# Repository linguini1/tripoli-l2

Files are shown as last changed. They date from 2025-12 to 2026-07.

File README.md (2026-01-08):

# Tripoli L2 Certification Rocket

<p align="center">
    
    <br/>
    Mission Patch
</p>

This repository contains the design files for my Tripoli L2 certification
rocket. My desire is to publicize the design files with a free-to-access intent
such that others in the rocketry hobby can benefit from them.

<p align="center">
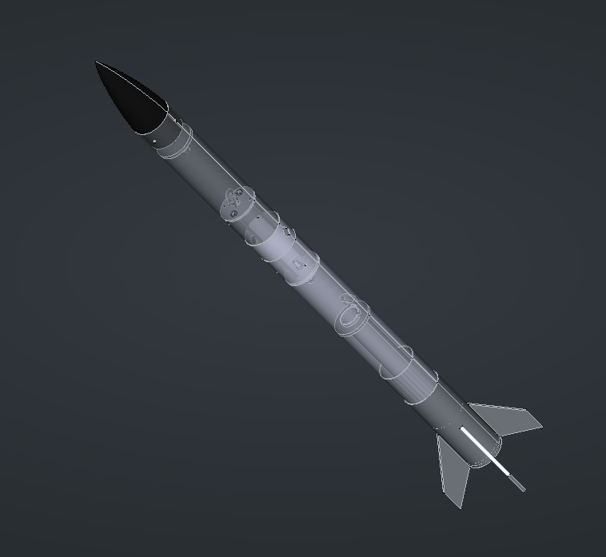
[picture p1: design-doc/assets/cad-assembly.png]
    
    <br/>
    Tripoli L2 CAD Assembly
</p>

## Design Document

The primary design document is located in the [design-doc
directory](./design-doc). It contains the requirements, design and analysis of
the rocket along with some design files in a cohesive layout.

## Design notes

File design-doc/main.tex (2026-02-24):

\documentclass[11pt]{article}

\def\doctitle{Analysis and Design of a Tripoli L2 Certification Rocket}

\usepackage{amssymb}
\usepackage{amsmath}
\usepackage{float}
\usepackage{graphicx}
\usepackage{listings}
\usepackage{enumitem}
\usepackage[
    pdftitle={\doctitle},
    colorlinks=false,
    allbordercolors={0 0 0},
    citebordercolor={1 1 1}, % No border for citations %
    pdfborderstyle={/S/U/W 1},
    linktoc=all,
]{hyperref}
\usepackage[nameinlink]{cleveref} % For hyperlinked references
\usepackage[letterpaper, margin=1in]{geometry}

% Add bibliography in IEEE
\usepackage[style=ieee]{biblatex}
\addbibresource{bibliography.bib}

% Add glossary entries
\usepackage[acronym,nogroupskip,nonumberlist]{glossaries}
\input{sections/glossary.tex}
\makeglossaries

% Remove paragraph indentation and use newline to separate instead. %
\usepackage[parfill]{parskip}
\setlength{\parindent}{0cm}

\title{\doctitle}
\author{
    Matteo Golin \\
    \texttt{matteo.golin@gmail.com}
}
\date{
    Created: December 27, 2025 \\
    Updated: \today
}

\begin{document}

% TITLE

\maketitle
\begin{center}
    
\end{center}
\pagebreak

% ABSTRACT

\input{sections/abstract.tex}
\pagebreak

% FRONT MATTER

{
	% No link styling in the TOC
	\hypersetup{hidelinks}
	\tableofcontents
	\pagebreak
	\listoffigures
	\pagebreak
	\listoftables
}
\pagebreak

% INTRODUCTION

\input{sections/introduction.tex}

% SECTIONS

\input{sections/requirements.tex}
\input{sections/overview.tex}
\input{sections/design/design.tex}
\input{sections/bom.tex}

\pagebreak

% GLOSSARY

\printglossary[title={Glossary}]
\printglossary[type=\acronymtype,title={Acronyms}]
\pagebreak

% BIBLIOGRAPHY

\printbibliography
\pagebreak

% APPENDIX

\input{appendix/index.tex}

\end{document}

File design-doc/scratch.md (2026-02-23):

# Scratch Ideas

## Motor

38mm motor is the final choice. It is easier to obtain in Canada and will also
be cheaper.

The motor needs a retention method. Based on what I've heard from others who
have done an L2, a retention method similar to an Aeropack retainer (like my L1)
is suitable.

## Recovery

Dual deploy, dual break. Drogue at apogee, main halfway down. Switchband coupler
to house deployment avionics, which will consist of between \[1, 2\] barometric
altimeters capable of deploying 2 deployment charges each (main and drogue) at
different altitudes. Altimeters will also need to be capable of deploying after
a set time-limit as an extra precaution.

Deployment will use black-powder charges detonated by e-matches.

## Airframe

Nosecone is PETG 3D-printed. Body tubes are fiberglass sock layup (6 layers,
light, 3in). Fins will be plywood through-wall so that I can have better thrust
transfer. Other materials are acceptable if I can acquire them.

[Fiberglass sock](https://sollercompositesllc.com/product/natural-uncolored-3-light-fiberglass-sleeves/)

I will have 2x 36" cardboard mandrels for the layup. The airframe body tubes
are:
* Forward: 14in
* Aft: 26in
* Switch-band exterior: 2in

In order to waste less sock, I will have one 18in mandrel for the forward +
switch-band layup. Then, I will use a 28in mandrel for the aft tube (inch of
slack on either end). Then there is an 8in coupler section for which I will
3D-print a 10in mandrel (to get the correct dimensions to be a coupler).

$18 + 28 + 10 = 56$ inches of total tube length. $58 \times 6$ for 6 layers gives
336 inches of sock required (28 ft). I will probably want to buy at least 30ft
(since that gives a discount on Soller anyways), but I may also want to account
for a complete screw-up on one of the tubes (let's say the coupler, since that
will be my test-tube). That would amount to 420in or 35 ft of stock.

## Avionics

\[1,2\] barometric altimeters for recovery deployment. Must perform on-board
altitude/charge detonation logging, be capable of firing two deployment charges
each and have some kind of audio indicator of arming and continuity check.

The avionics bay must be capable of supporting a redundant deployment
configuration.

The GPS tracker will go in the nosecone and at minimum must be capable of
providing coordinates of the rocket's landing location over long-range radio.

# Parts

* [Motor mount tube](https://www.allrockets.ca/Build/Motor-Tubes/P/38)
* [Motor retainer (for specific motor mount tube)](https://www.allrockets.ca/Build/Motor-Retainers/38-mm-P)
* [Eyebolts x4](https://www.allrockets.ca/Build/Swivels-Links/Eye-Bolt-1)
* [Rail buttons](https://www.allrockets.ca/Build/Rail/Delrin-Rail-Gudes/1010-Airframe)
* [Body tube (for layup) x2](https://www.allrockets.ca/Build/Body-Tubes/30)
* [12in drogue](https://www.allrockets.ca/Build/Parachutes/Nylon-Red-12?cPath=19_212&)
* [36in main](https://www.allrockets.ca/Build/Parachutes/36)
* [Kevlar shock cord (?m)](https://www.allrockets.ca/Build/Shock-Cords/Kevlar-1500)
* [12x12 chute protector x2](https://www.allrockets.ca/Accessories/Chute-Protector-12)
* [1kg black PETG](https://www.amazon.ca/ELEGOO-Filament-Printing-Dimensional-Cardboard/dp/B0CMC8CDFN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)
* [10-24x12in threaded rod x2](https://www.homedepot.ca/product/paulin--10-24-x-12-inch-fully-threaded-steel-rod-zinc-plated-unc/1000798814)

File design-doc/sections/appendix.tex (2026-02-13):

\section{Technical Drawings}

These are the technical drawings that describe the dimensions of each rocket
component needed for assembly.

\subsection{Nosecone}

\begin{figure}[H]
	\centering
	
	\caption{Technical drawing of the nosecone model}
\end{figure}

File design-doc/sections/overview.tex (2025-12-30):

\section{Design Overview}

This rocket will be a dual break, dual deploy rocket. It is technically only
necessary to have a single-break, single-deploy system, but this design choice
will teach me more about what's required for an L3 certification as well as
reduce any ability for the rocket to drift after apogee.

Since the rocket is dual break, the design for the avionics bay is going to be a
switch-band. This is a common choice for dual-deploy rocket and also looks very
simple to integrate (to me). Since the entire switch-band assembly is removable,
it will be easy to fiddle with when installing the avionics and can be replaced
entirely if I do something silly like drill the arming holes terribly wrong or
discover I need to re-arrange the entire avionics section. The primary
inspiration for the design the switchband avionics section is the design from
Joe Barnard's \textit{Send It!} rocket. \cite[\nopp 4:14]{bps-sendit} I like
the design choice of using Wago lever connectors for deployment charges to avoid
a screwdriver \cite[\nopp 5:47]{bps-sendit}, but I will need to come up with a
better solution than just epoxying the connectors to the bulkhead in case one
needs to be replaced. The bulkheads will be pressure sealing in order to prevent
the deployment charges from affecting the barometric altimeters inside the
avionics bay, and also to make sure that the correct volume of the rocket is
pressurized to deploy the chutes. Most of the configurations I have seen use a
small lip on both bulkheads so that they rest on the switchband coupler tube. I
have been told that using a o-ring to seal the pressure is overkill.

\begin{figure}[H]
	\centering
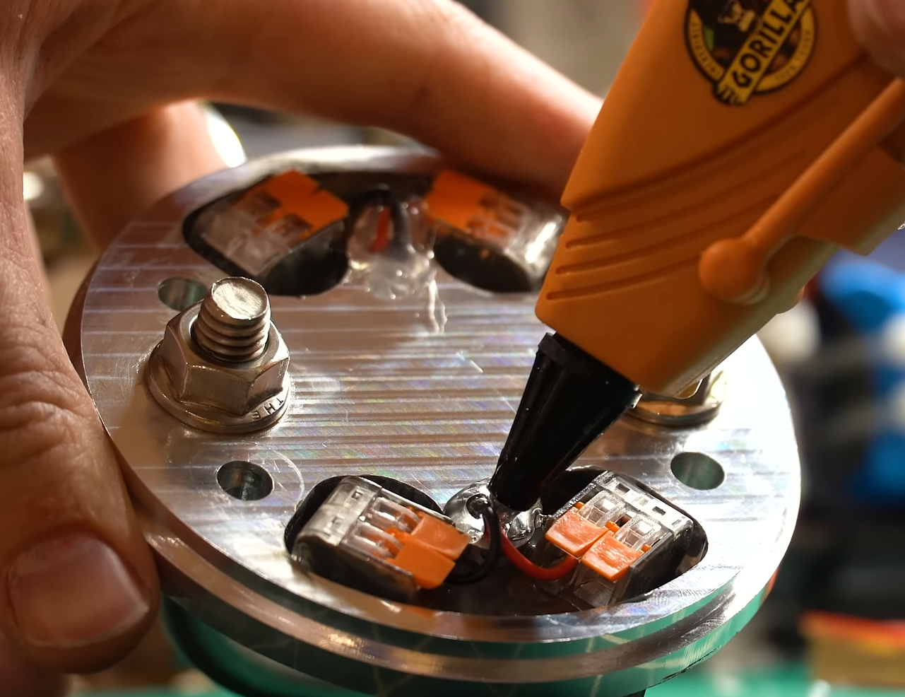
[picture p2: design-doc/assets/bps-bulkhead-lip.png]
	
	\caption{Aluminum bulkhead for switchband with a visible lip for the coupler
    tube \cite[\nopp 6:17]{bps-sendit}}
\end{figure}

For deployment electronics, I will not fly a redundant configuration if I can
help it (the Tripoli L2 rules do not require it \cite{tripoli-l2}) in order to
save costs, but I would like the avionics bay design to be capable of supporting
a redundant configuration if necessary. This should mostly be an issue of wiring
and extra space in the avionics bay, so it is unlikely to be a large
undertaking.

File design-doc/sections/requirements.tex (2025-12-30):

\section{Design Requirements}

The primary requirements for the rocket are derived from the Tripoli L2
certification requirements in \cite{tripoli-l2}, the L2 experience flight
requirements as per \cite[\nopp 4]{tripoli-l3} and the Tripoli Unified Safety
Code. \cite{tripoli-safety} These requirements are critical to meet in order to
achieve the goal of this rocket, which is to obtain my L2 certification and
complete the experience requirements towards an L3.

The secondary requirements for the rocket are derived from the desire to lower
the risk of failing the certification process and to reduce the amount of effort
required for assembly, pre-flight preparation and post-flight recovery.

The tertiary requirements for the rocket are derived from the desire to learn
some new skills and have a somewhat cool certification rocket to be proud of.
These requirements can be given up, just at my own disappointment.

\subsection{Primary Requirements}

\begin{enumerate}[label={R 1.\arabic*}]
	\item The rocket must be of conventional design (stabilized by fins and
	      recovered under parachutes) \cite[Airframe]{tripoli-l2}
	\item The rocket must be not be entirely 3D printed \cite[Airframe]{tripoli-l2}
	\item The rocket must be recovered by parachute \cite[Recovery]{tripoli-l2}
	\item The rocket must have a descent rate less than 11 meters per second
	      \cite[\nopp 11-1]{tripoli-safety}
	\item The rocket's recovery deployment must be electronically controlled
	      \cite[4]{tripoli-l3}
	\item All components of the rocket must be connected and recovered in one
	      assembly \cite[Non-Certification]{tripoli-l2}
	\item The rocket must be powered by a single J, K or L motor \cite[Motor]{tripoli-l2}
	\item The rocket must have a thrust to weight ratio of 5:1 or more \cite[\nopp 7-1.4]{tripoli-safety}
	\item The rocket must have a stable ascent \cite[Certification Flight]{tripoli-l2}
	\item The rocket must have a marked center of pressure \cite[7-1.2]{tripoli-safety}
	\item The rocket must have a marked center of gravity \cite[7-1.2]{tripoli-safety}
\end{enumerate}

\subsection{Secondary Requirements}

\begin{enumerate}[label={R 2.\arabic*}]
    \item The rocket must fly a 38mm motor
	\item The rocket must be capable of recovery deployment both via motor
	      ejection charge and electronic control, under the assumption that both
	      fire during flight.
	\item Continuity of deployment charge channels must be verifiable at the
	      time of arming on the pad.
	\item The rocket must have a GPS tracker so that its final landing location
	      can be obtained while tracking its flight from the vertical launch area.
	\item The deployment altimeter must be equipped with a barometer for
	      higher accuracy altitude estimation.
	\item The deployment system must be capable of firing deployment charges
	      both at a specific altitude and after a fixed time since lift-off in
	      the case of failure to detect altitude.
	\item The GPS tracker frequency must be capable of being easily changed on
	      the pad.
	\item The deployment altimeter must log timestamped altitude measurements
	      during flight.
	\item The deployment altimeter must log timestamped deployment event
	      signals.
	\item All locations for connecting shock-cord which need to be accessed
	      during pre-flight preparation must be easily accessible by hand.
	\item Rail buttons must be capable of being installed using the provided
	      flanges.
	\item One rail button must be placed as low as possible on the rocket
	      airframe, and the other must be placed at the expected center of
	      gravity.
	\item The GPS tracker must have a transmission range that exceeds the
	      maximum expected drift of the rocket.
	\item All 3D printed parts and assembly tools must be printable on a
	      $220\times220\times250$ mm print bed.
	\item The deployment electronics bay must have sufficient venting holes
	      for access to the atmosphere during flight.
	\item All separate volumes of the rocket must have sufficient venting holes
	      to prevent unintended separation.
	\item The rocket avionics bay must be capable of supporting a redundant
	      deployment configuration.
\end{enumerate}

\subsection{Tertiary Requirements}

\begin{enumerate}[label={R 3.\arabic*}]
	\item At least one part of the airframe should be made of a composite material
	      (either fiberglass or carbon fiber is acceptable)
	\item No fastener should be a Phillips head
	\item The rocket should be easy to manufacture
    \item The rocket might have a boat-tail
\end{enumerate}

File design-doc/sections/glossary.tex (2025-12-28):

\newacronym{pcb}{PCB}{Printed Circuit Board}

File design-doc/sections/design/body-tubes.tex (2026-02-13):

\subsection{Body Tubes}

The body tubes for the rocket are 3in diameter and made of fiberglass composite.

\subsubsection{Manufacture}

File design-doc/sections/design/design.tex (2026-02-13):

\section{Design}

\input{sections/design/nosecone.tex}
\input{sections/design/body-tubes.tex}
\input{sections/design/switchband.tex}
\input{sections/design/fincan.tex}
\input{sections/design/recovery.tex}
\input{sections/design/avionics.tex}

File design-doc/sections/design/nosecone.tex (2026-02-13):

\subsection{Nosecone}

The nosecone is a Von Karmaan nosecone shape. The length of the nose is 7
inches, and the length of the shoulder is 2 inches. The shoulder thickness is
$\frac{1}{4}$ inch.

The height of the nosecone was selected to be within the ~225mm print-height
limit for most consumer printers.

\subsubsection{Manufacture}

The nosecone of the rocket will be manufactured out of PETG for simplicity. This
allows the (relatively complex) shape to be made on a consumer 3D printer, which
is generally accessible. It does not require an "advanced" 3D printer which has
the capability to print in filaments like ABS. PETG also has the property of
being radio transparent, which is required for a nose-cone GPS tracker.

The nosecone should be printed using gyroidal infill for high strength. It is
also recommended to use a minimum of 4 vertical walls in the slicer settings for
durability.

\subsection{Assembly}

The nosecone is affixed to the forward body tube using 4 radial M3 screws. The
nosecone is fitted with 4 heat-set inserts evenly space along the shoulder. This
allows the nosecone to be removed, but also tightly affixed for flight.

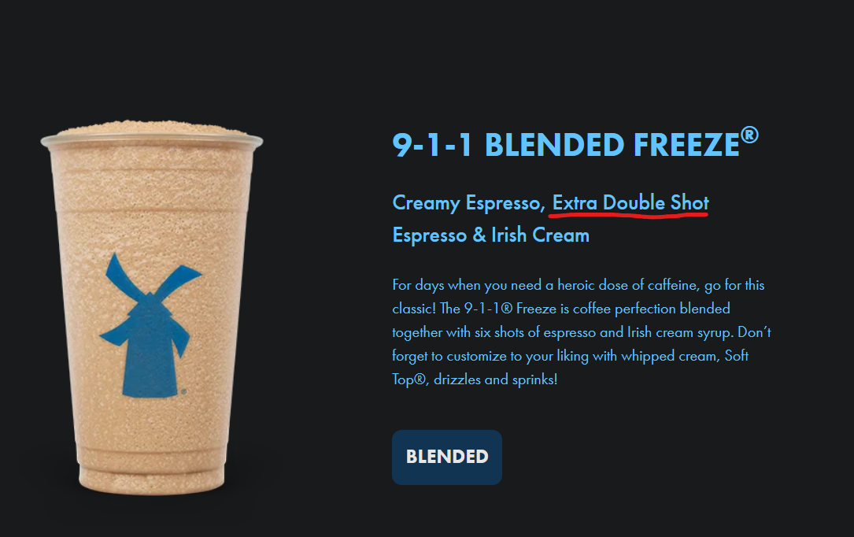
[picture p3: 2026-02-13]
design-doc/assets/dbros.png

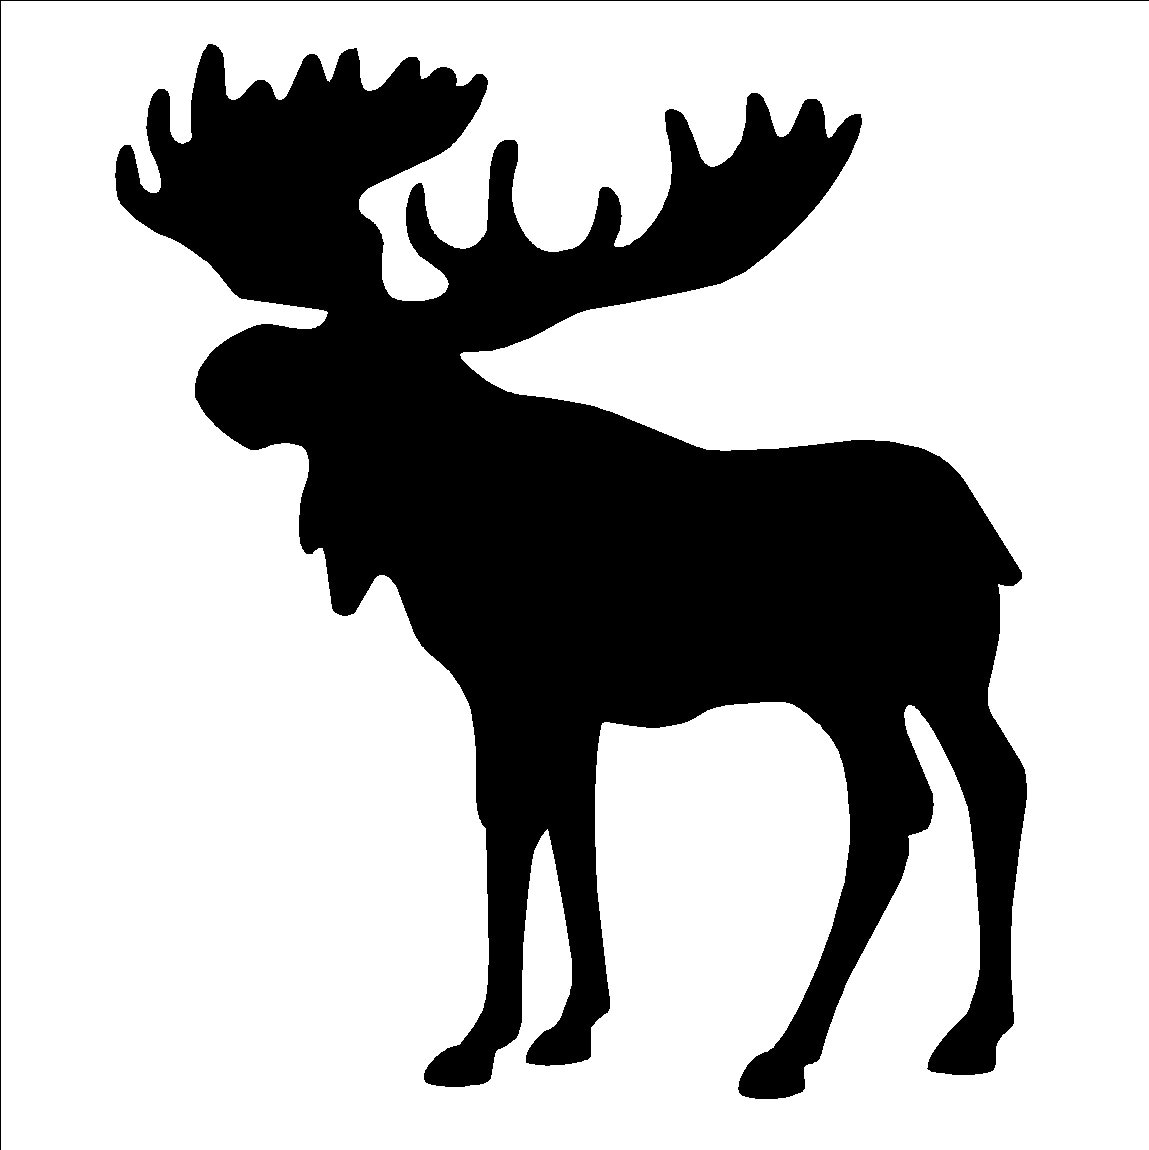
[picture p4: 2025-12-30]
livery/moose.jpg

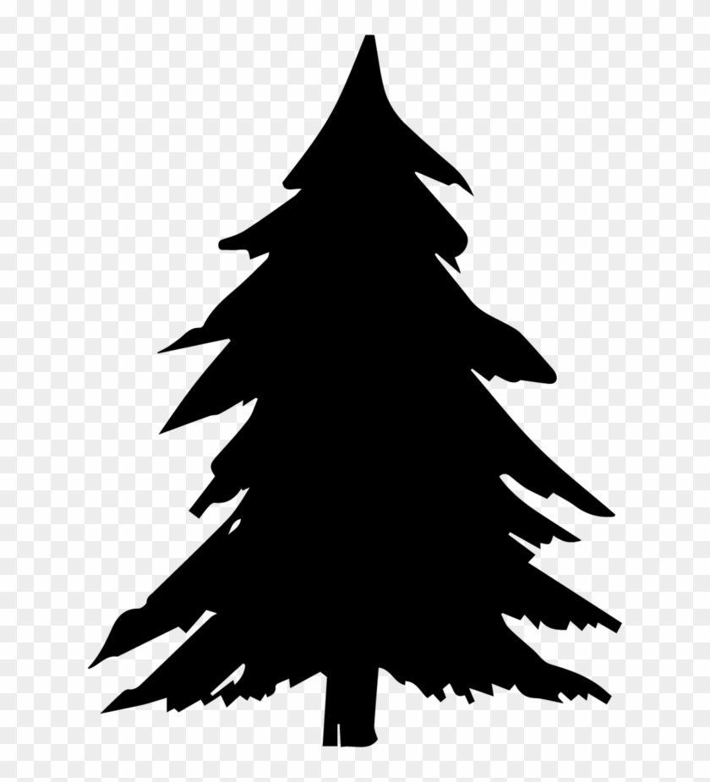
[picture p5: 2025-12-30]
livery/pinetree.png

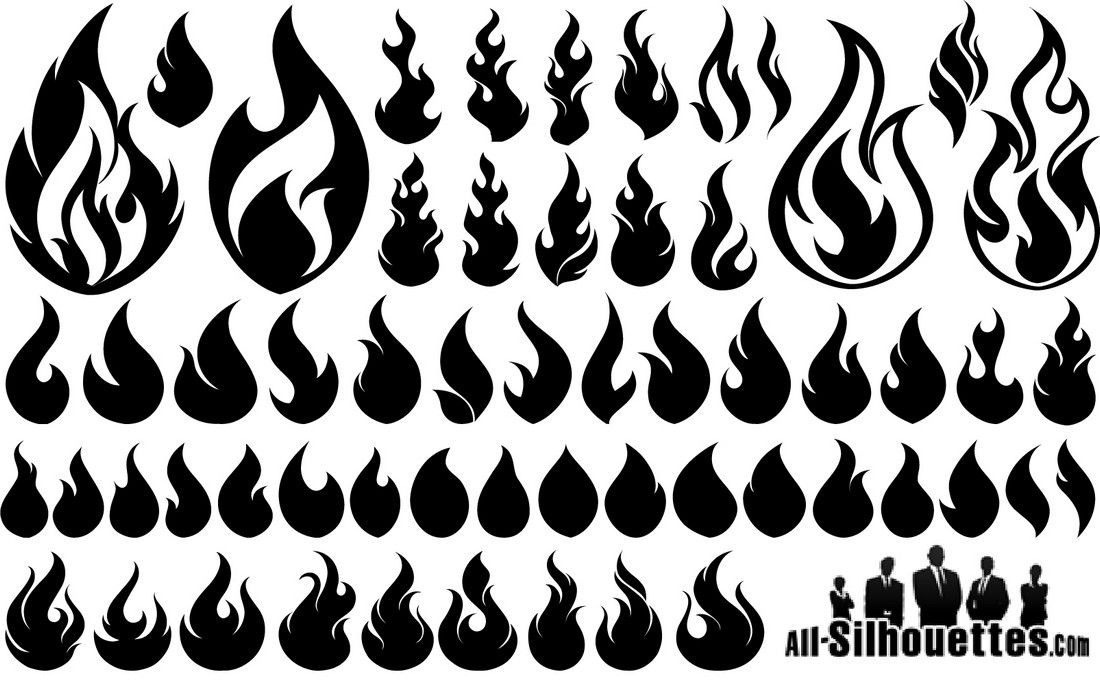
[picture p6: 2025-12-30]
livery/flames.jpg

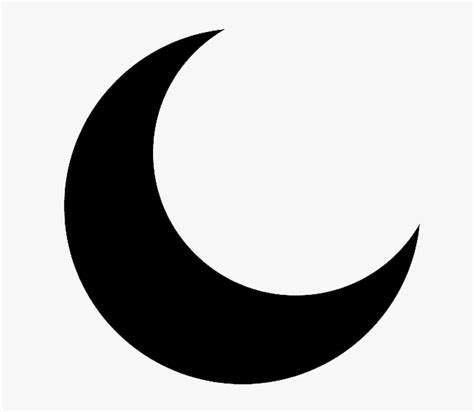
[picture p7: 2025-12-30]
livery/moon.jpg

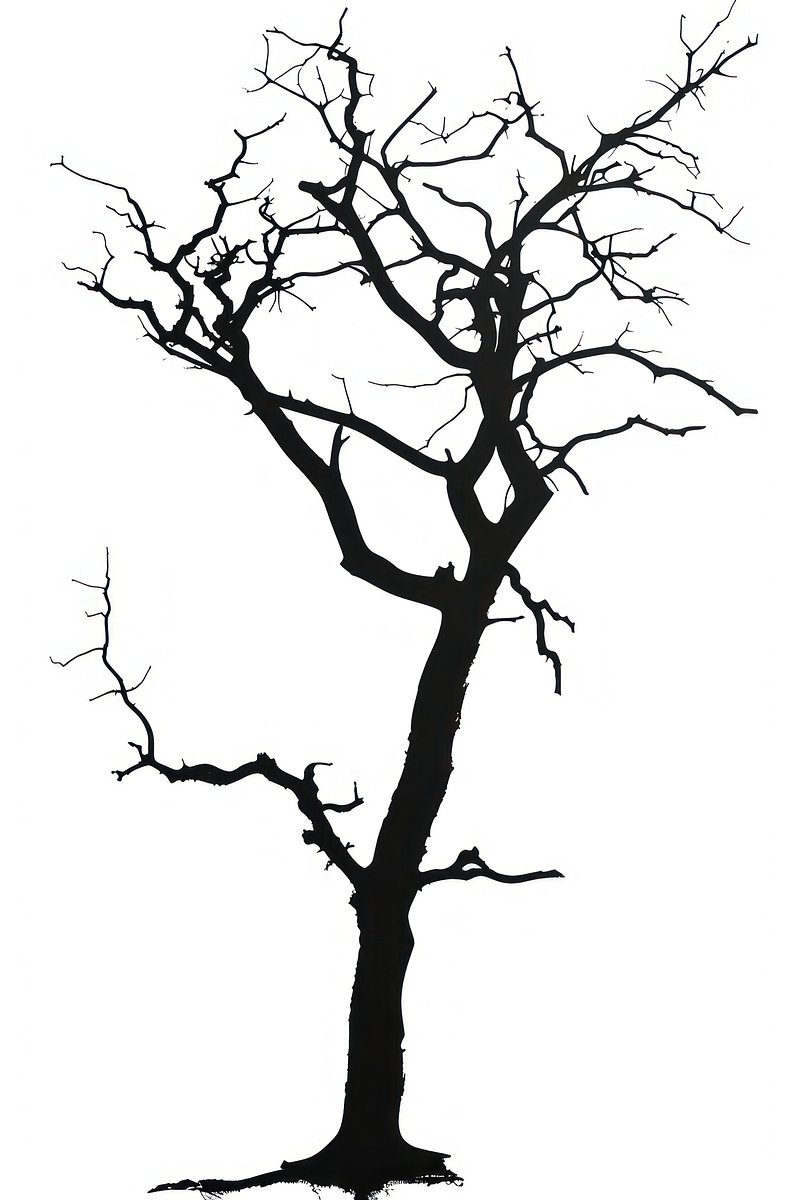
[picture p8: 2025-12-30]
livery/deadtree.jpg

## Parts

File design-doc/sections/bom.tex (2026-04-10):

\section{Bill Of Materials}

This section contains the bill of materials required to manufacture the entire
rocket. Links are provided where applicable.

\begin{table}
    \centering
    \begin{tabular}{| p{2in} | c | p{1in} | p{1in} | c |}
        \hline
        Name                       & Quantity & Use                     & Comment                                   & Link                                                                                                                                                                                                                                                                                                                                                                                                                                                                                                                                                                                                          \\
        \hline
        Motor mount tube           & 1        & Motor                   &                                           & \href{https://www.allrockets.ca/Build/Motor-Tubes/P/38}{Link}                                                                                                                                                                                                                                                                                                                                                                                                                                                                                                                                                 \\
        \hline
        Motor retainer             & 1        & Motor                   & Specific Aeropack for the tube            & \href{https://www.allrockets.ca/Build/Motor-Retainers/38-mm-P}{Link}                                                                                                                                                                                                                                                                                                                                                                                                                                                                                                                                          \\
        \hline
        1/4" Eyebolt               & 4        & Recovery tether         &                                           & \href{https://www.allrockets.ca/Build/Swivels-Links/Eye-Bolt-1}{Link}                                                                                                                                                                                                                                                                                                                                                                                                                                                                                                                                         \\
        \hline
        10-24x12in threaded rod    & 2        & Switchband              & Only needs 9in                            & \href{https://www.homedepot.ca/product/paulin--10-24-x-12-inch-fully-threaded-steel-rod-zinc-plated-unc/1000798814}{Link}                                                                                                                                                                                                                                                                                                                                                                                                                                                                                     \\
        \hline
        10-24 nuts                 & 8        & Switchband              &                                           & ?                                                                                                                                                                                                                                                                                                                                                                                                                                                                                                                                                                                                             \\
        \hline
        10-24 washers              & 8        & Switchband              &                                           & ?                                                                                                                                                                                                                                                                                                                                                                                                                                                                                                                                                                                                             \\
        \hline
        PETG filament (kg)         & 1        & Nosecone                & 3D print                                  & \href{https://www.amazon.ca/gp/product/B0F4KBJ3NC/ref=ox_sc_act_title_1?smid=AHDS16DQS1BPW                                               & psc=1}{Link}                                                                                                                                                                                                                                                                                                                                                                                                                                                       \\
        \hline
        M3 heat set inserts        & 4        & Nosecone                & Buy extra                                 & \href{https://www.amazon.ca/HANGLIFE-Heat-Set-Threaded-Printing-Components/dp/B0CS6VZYL8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                   & dib=eyJ2IjoiMSJ9.sDUzEMnqixdlRk6CED6yPxFfnnyoHRCo4DXONztL_yoDdRwBUW07LO2BYH-BUX8_f6zP7bTlp2OKi4O_n5_WIkT6HDTWC_Z1NqD8kD7HLp0lWkBUb2qO49IlqxbGe2EBGMrCf43E33SYiH8rpqTdX25_PQk8P469mSpYUaPqmqJ_kYF4dBBL0dmp7k-E-xb761G8eJmxBhQuF6_h5mDDGXC1HA6R9DqmHDYdcEVRBFLuLIDfz711hRHAl0u-s_zllHxYQ11G2FWEOJ6WppuTE6nDpEA4cOiujgIbMNOuK8g.GpvBhznhn0SzYbV8_LBgFcJHMEnSJuaAvhTADr7edWs & dib_tag=se & keywords=m3+heat+set+inserts & qid=1771868162 & sprefix=m3+heat+set+insert %2Caps%2C127&sr=8-6}{Link} \\
        \hline
        M3x8mm socket cap screw    & 4        & Nosecone                & Buy extra                                 & ?                                                                                                                                                                                                                                                                                                                                                                                                                                                                                                                                                                                                             \\
        \hline
        3in cardboard tube         & 2        & Body tube layup mandrel &                                           & \href{https://www.allrockets.ca/Build/Body-Tubes/30}{Link}                                                                                                                                                                                                                                                                                                                                                                                                                                                                                                                                                    \\
        \hline
        West systems 206 epoxy kit & 1        & Layups and assembly     &                                           & \href{https://www.leevalley.com/en-ca/shop/tools/supplies/adhesives/glue/20016-west-system-epoxy-kits?item=54Z2001}{Link}                                                                                                                                                                                                                                                                                                                                                                                                                                                                                     \\
        \hline
        West systems 407 filler    & 1        & Fillets                 &                                           & \href{https://www.leevalley.com/en-ca/shop/tools/supplies/adhesives/glue/102525-fairing-filler-for-west-system-epoxy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}{Link}                                                                                                                                                                                                                                                                                                                                                                                                                                                                      \\
        \hline
        Fiberglass sock (ft)       & 40       & Airframe                &                                           & \href{https://sollercompositesllc.com/product/natural-uncolored-3-0in-med-fiberglass-sleeves/}{Link}                                                                                                                                                                                                                                                                                                                                                                                                                                                                                                          \\
        \hline
        Plywood                    & ?        & Fins, bulkheads         & Could be substituted for another material & ?                                                                                                                                                                                                                                                                                                                                                                                                                                                                                                                                                                                                             \\
        \hline
        Kevlar shock cord (ft)     & ?        & Recovery                &                                           & \href{https://www.allrockets.ca/Build/Shock-Cords/Kevlar-1500A}{Link}                                                                                                                                                                                                                                                                                                                                                                                                                                                                                                                                         \\
        \hline
        15in parachute             & 1        & Drogue                  &                                           & \href{https://www.allrockets.ca/Build/Parachutes/Nylon-Red-12?cPath=19_212\&}{Link}                                                                                                                                                                                                                                                                                                                                                                                                                                                                                                                           \\
        \hline
        36in parachute             & 1        & Main                    &                                           & \href{https://www.allrockets.ca/Build/Parachutes/36}{Link}                                                                                                                                                                                                                                                                                                                                                                                                                                                                                                                                                    \\
        \hline
        Swivel link                & 2        & Parachutes              &                                           & \href{https://www.allrockets.ca/Build/Swivels-Links/Swivel-8}{Link}                                                                                                                                                                                                                                                                                                                                                                                                                                                                                                                                           \\
        \hline
        3/16" Quick link           & ?        & Parachutes              &                                           & \href{https://www.allrockets.ca/Build/Swivels-Links/Quick-Link-800}{Link}                                                                                                                                                                                                                                                                                                                                                                                                                                                                                                                                     \\
        \hline
        Rail buttons               & 1        & Rail mounting           & Two buttons per pack                      & \href{https://www.allrockets.ca/Build/Rail/Delrin-Rail-Gudes/1010-Airframe}{Link}                                                                                                                                                                                                                                                                                                                                                                                                                                                                                                                             \\
        \hline
        Wago clips                 & 8        & Deployment electronics  &                                           & ?                                                                                                                                                                                                                                                                                                                                                                                                                                                                                                                                                                                                             \\
        \hline
    \end{tabular}
    \caption{Bill of materials}
\end{table}

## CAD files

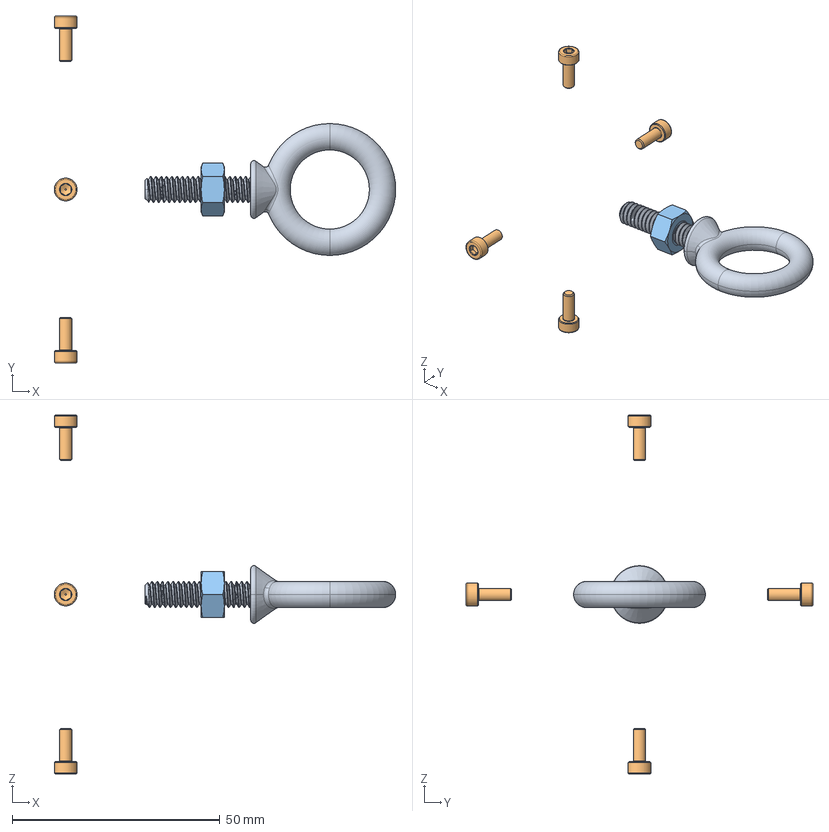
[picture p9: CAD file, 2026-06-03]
cad/ForwardAssembly.FCStd
82.2 x 83.5 x 86.4 mm
1/4-1in Eyebolt
M3x8-Screw x 4
1/4in-Nut

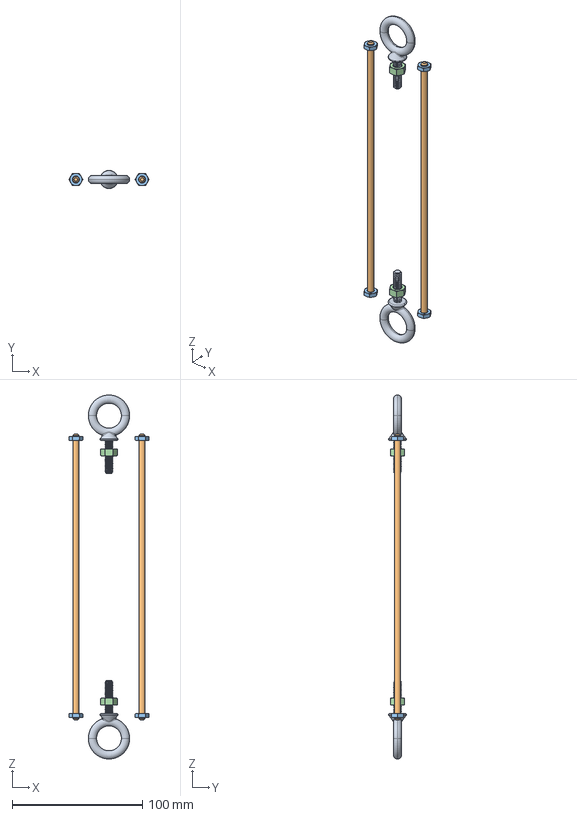
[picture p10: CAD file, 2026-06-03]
cad/AvBayAssembly.FCStd
61.6 x 13.9 x 279.4 mm
1/4in-1in Eyebolt x 2
#10x219.54999999999998-ThreadedRod x 2
#10-Nut x 4
1/4in-Nut x 2

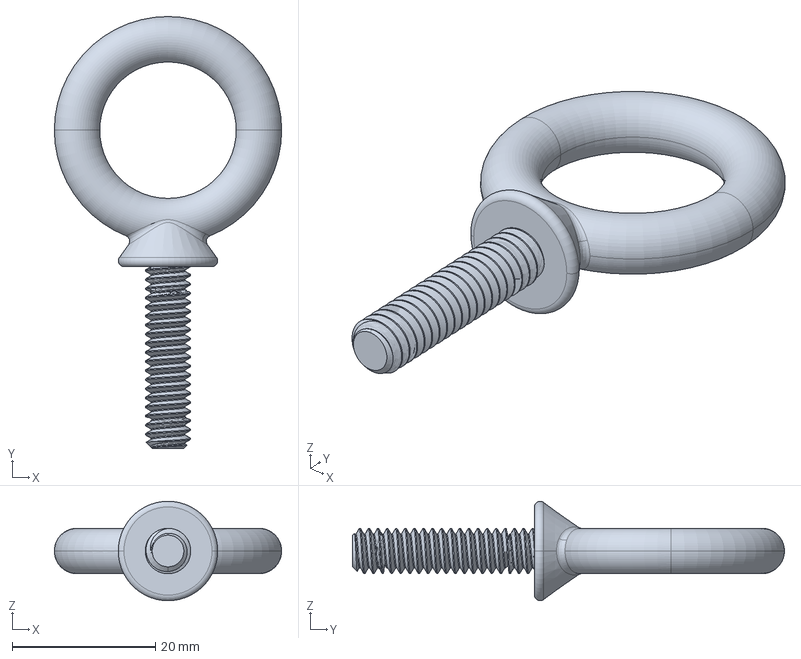
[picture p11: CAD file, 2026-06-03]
cad/AftAssembly.FCStd
31.8 x 60.3 x 13.9 mm

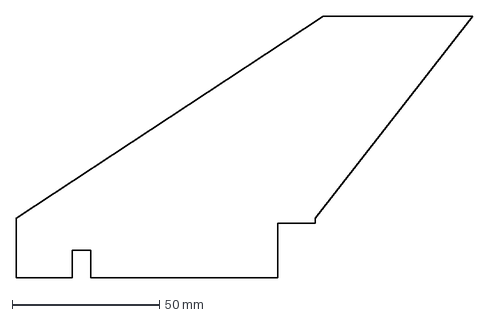
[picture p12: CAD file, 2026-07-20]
cad/Components-FinOutline.dxf
155.2 x 88.8 mm

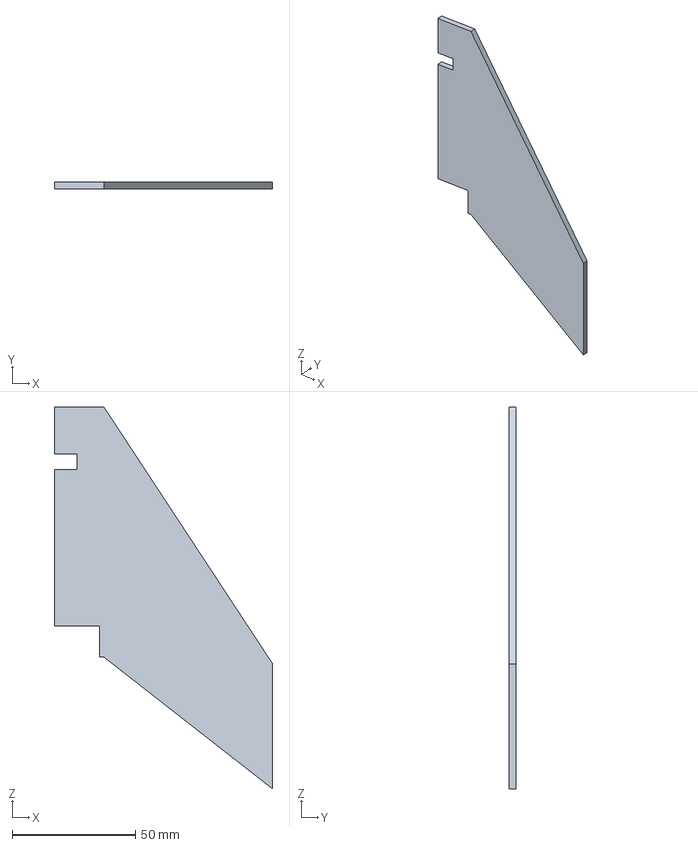
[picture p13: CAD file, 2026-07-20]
cad/Components.FCStd
88.8 x 3.00 x 155.2 mm

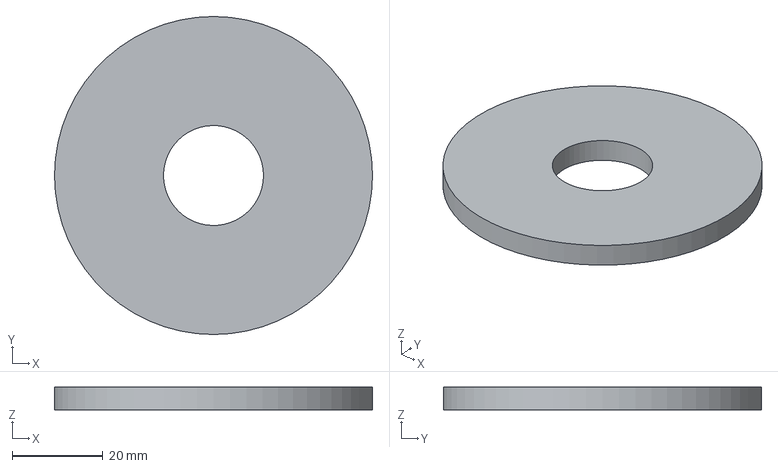
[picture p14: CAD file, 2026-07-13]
cad/Components-CouplerMandrelCenteringRing.step
70.0 x 70.0 x 5.00 mm

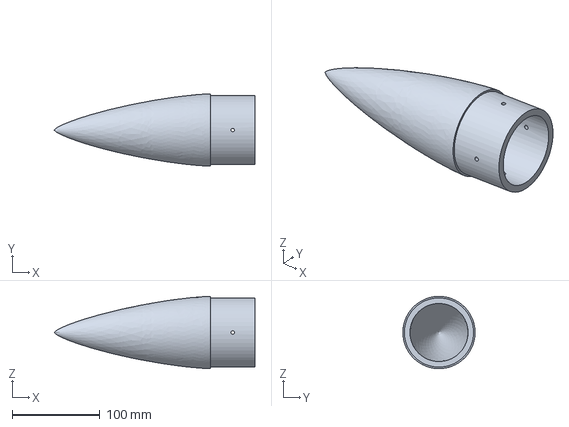
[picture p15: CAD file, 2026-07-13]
cad/Components-Nosecone.step
228.6 x 82.2 x 82.2 mm

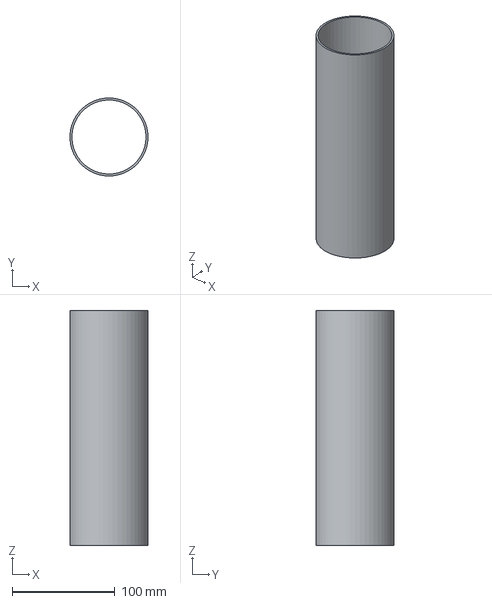
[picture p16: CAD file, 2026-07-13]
cad/Components-CouplerMandrel.step
75.9 x 76.0 x 228.6 mm

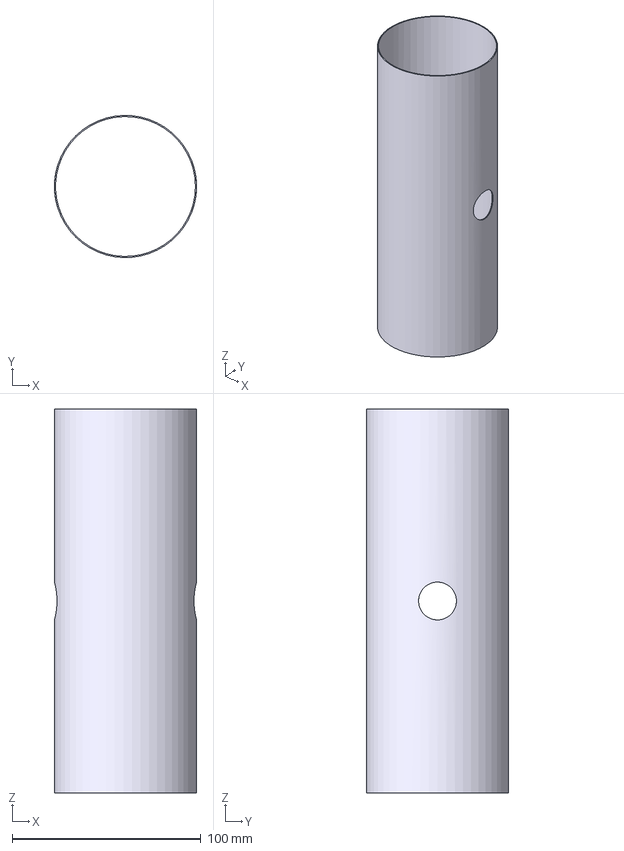
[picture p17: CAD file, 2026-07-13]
cad/Components-AvBayInt.step
75.2 x 75.2 x 203.2 mm

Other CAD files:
cad/RocketAssembly.FCStd
cad/Components-Fin.step
cad/8891T72_316 Stainless Steel Eyebolt.STEP

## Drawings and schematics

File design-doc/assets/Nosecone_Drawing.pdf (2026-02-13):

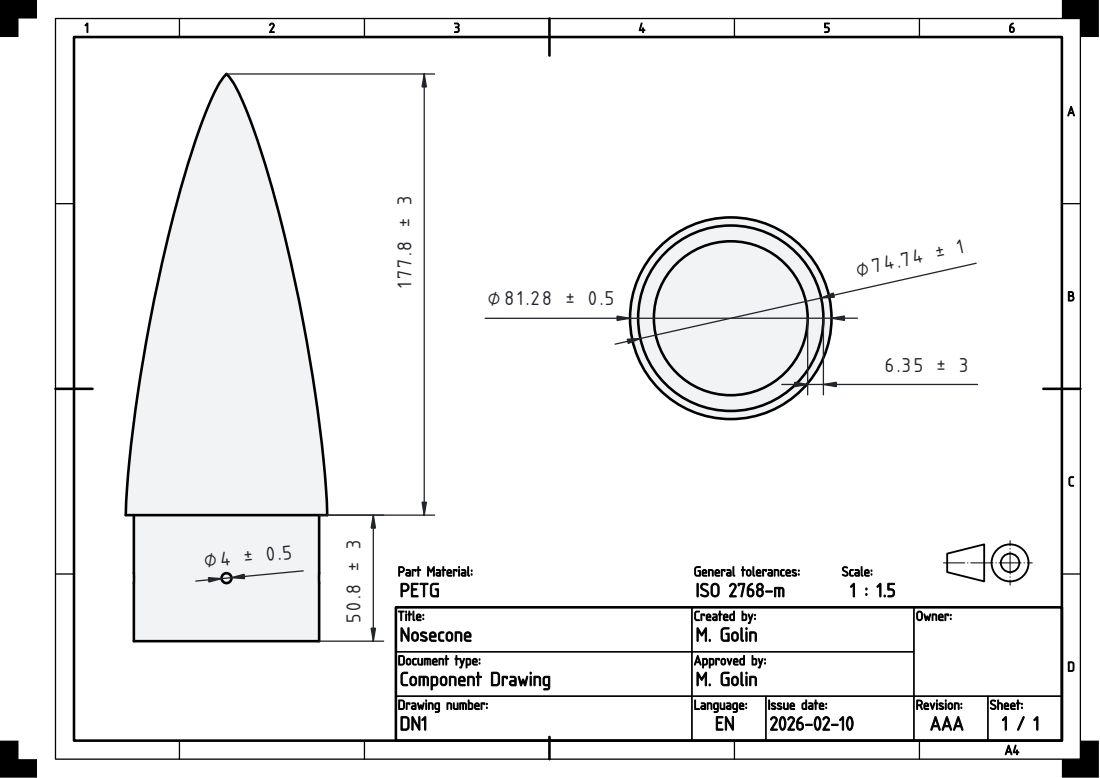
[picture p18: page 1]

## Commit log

2025-12-30 Assets for livery (mission patch)
    [chicken-house.gbr, deadtree.gbr, flame.gbr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]
2025-12-30 Some preliminary CAD modelling
    [Aft.FCStd, AvBay.FCStd, Components.FCStd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]
2026-01-01 Updated CAD model. Are 1/4in eyebolts too big? And is there enough room for chutes?
    [8891T72_316 Stainless Steel Eyebolt.STEP, Aft.FCStd, AftAssembly.FCStd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]
2026-01-01 Slightly more fleshed out design. Made rocket more stable, picked out some parts.
    [AftAssembly.FCStd, AvBayAssembly.FCStd, Components.FCStd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]
2026-01-06 Small changes
    [AftAssembly.FCStd, RocketAssembly.FCStd]
2026-01-08 CAD assembly image
2026-01-08 Correct tube ID based on OD of cardboard tubes used for layup. Layup thickness parameter can be tweaked.
    [AvBayAssembly.FCStd, Components.FCStd, ForwardAssembly.FCStd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]
2026-01-08 OpenRocket correct body tube IDs based on layup.
2026-01-14 Introduced 3D printed mandrel for coupler to make sure that regardless of layup thickness, I can have an exact coupler OD to body tube ID match to sand down.
    [AftAssembly.FCStd, AvBayAssembly.FCStd, Components.FCStd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]
2026-02-13 Added some drawings.
    [AftAssembly.FCStd, AvBayAssembly.FCStd, Components.FCStd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]
2026-02-22 Change tip-to-tip layup surface mount fins to through-wall fins.
    [AftAssembly.FCStd, AvBayAssembly.FCStd, Components.FCStd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]
2026-02-22 Don't model shear pin holes
    [AftAssembly.FCStd, AvBayAssembly.FCStd, Components.FCStd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]
2026-02-24 Increase drogue size, updated BOM
2026-04-10 Update fiberglass sleeve dimensions
    [AvBayAssembly.FCStd, Components.FCStd, ForwardAssembly.FCStd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]
2026-04-21 Updated with new fiberglass sleeve sizing and fiberglass fin sheets.
    [AvBayAssembly.FCStd, Components.FCStd, ForwardAssembly.FCStd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]
2026-04-21 Misc changes
    [AftAssembly.FCStd, AvBayAssembly.FCStd, Components.FCStd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]
2026-04-22 Some jig tools for doing the layup.
    [AftAssembly.FCStd, AvBayAssembly.FCStd, Components.FCStd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]
2026-06-03 Component changes
    [Components.FCStd]
2026-06-03 chore: update real layup thickness and fix all associated errors
    [AftAssembly.FCStd, AvBayAssembly.FCStd, Components.FCStd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]
2026-06-03 chore: fix broken nosecone part link
    [AftAssembly.FCStd, AvBayAssembly.FCStd, Components.FCStd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]
